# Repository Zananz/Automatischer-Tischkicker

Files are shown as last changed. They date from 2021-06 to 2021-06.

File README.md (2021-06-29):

<h1>Automatischer Tischkicker</h1>
<p>
1. <a href="https://github.com/Zananz/Automatischer-Tischkicker#beschreibung">Beschreibung</a><br>
2. <a href="https://github.com/Zananz/Automatischer-Tischkicker#funktionsweise">Funktionsweise</a><br>
3. <a href="https://github.com/Zananz/Automatischer-Tischkicker#anleitung">Anleitung</a><br>
</p>
<h2>Beschreibung</h2>
<p>Ein umgebauter Tischkicker welcher in der Lage ist Tore
automatisch zu zählen und Spielstände von bis zu 16 Spielern zu
Speichern.
</p>
<h2>Funktionsweise</h2>
<p>Der umgebaute Tischkicker verfügt über 2 Terminals mit jeweils
einem 2x16LCD-Display und 5 Schaltern. 4 der 5 Schalter dienen zur
Eingabe der Spieler-ID (ein max. vierstelliger Binärwert (0=0000,
1=0001 usw.)(daher 16 Spieler)), der verbleibende Schalter dient zum
bestätigen der ID.  Des weiten verfügt der Tischkicker über 2 rote
Buttons welche auf der jeweiligen Seite ein Tor (Punkt) abziehen.</p>
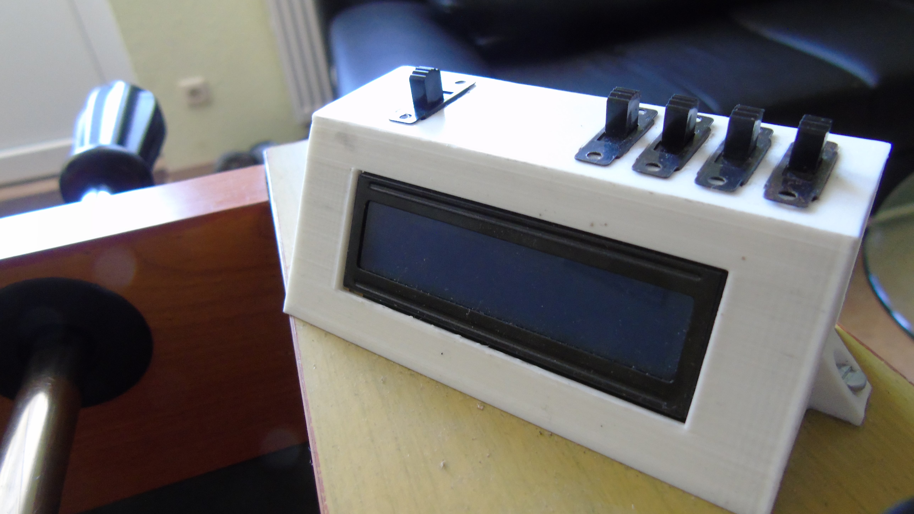
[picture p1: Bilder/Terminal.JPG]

<p>Tore werden mit Hilfe von Lichtschranken an der Ballführung
zwischen Tor und Ballausgabe gezählt.</p>
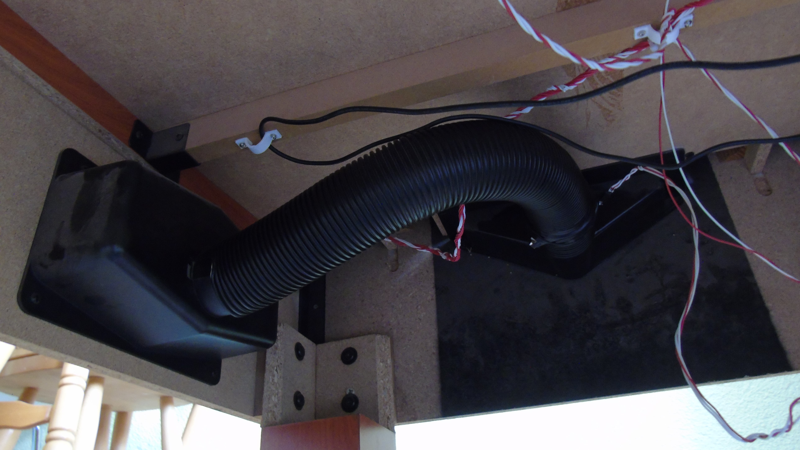
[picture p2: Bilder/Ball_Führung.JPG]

<p>Zur Ansteuerung der Komponenten wird ein Raspberry Pi pico verwendet welcher mit einer 3D-gedruckten <a href = "https://github.com/Zananz/Automatischer-Tischkicker/blob/main/3D-Modele/Halterung%20Platine.stl">Halterung</a> an der Unterseite des Tischkickers befestigt ist.</p>
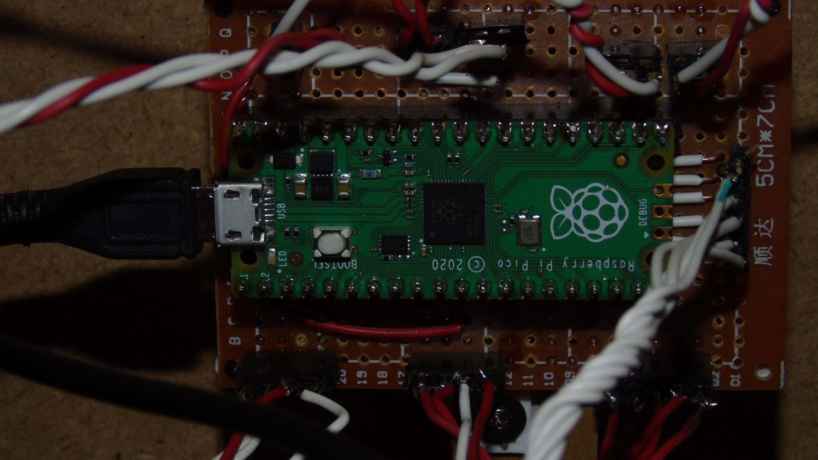
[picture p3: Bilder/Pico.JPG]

<h2>Anleitung</h2>
<h3>Hardware</h3>
<h4>Benötigt</h4>
<p>
&nbsp;&nbsp;&nbsp;&nbsp;1. <a href="https://www.reichelt.de/de/de/raspberry-pi-pico-rp2040-cortex-m0-microusb-rasp-pi-pico-p295706.html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">Raspberry Pi pico</a><br>
&nbsp;&nbsp;&nbsp;&nbsp;2. <a href="https://www.ebay.de/itm/353136370982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">2x 5V Laserdiode 6mm Ø</a><br>
&nbsp;&nbsp;&nbsp;&nbsp;3. <a href="https://www.ebay.de/itm/272853994103?chn=ps&mkevt=1&mkcid=28">2x Fotowiederstand</a><br>
&nbsp;&nbsp;&nbsp;&nbsp;4. <a href="https://www.ebay.de/itm/353160204184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">2x 16x2 LCD-Display + I2C Controller </a><br>
&nbsp;&nbsp;&nbsp;&nbsp;5. <a href="https://www.ebay.de/itm/333602388391?ssPageName=STRK%3AMEBIDX%3AIT&_trksid=p2060353.m2749.l2649">10x Schalter</a><br>
&nbsp;&nbsp;&nbsp;&nbsp;6. <a href="https://www.reichelt.de/arcade-button-mit-mikrostaster-rot-arc-button-rd-p225319.html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">2x Button 33mm Ø</a><br>
&nbsp;&nbsp;&nbsp;&nbsp;7. M3 Schrauben (4x 5mm, 4x ca.50mm), 4 Muttern<br>
&nbsp;&nbsp;&nbsp;&nbsp;8. <a href="https://www.ebay.de/itm/174035126580?chn=ps&mkevt=1&mkcid=28">Pin Header Male</a>, <a href="https://www.ebay.de/itm/174252775416?chn=ps&mkevt=1&mkcid=28">Pin Header Female</a><br>
&nbsp;&nbsp;&nbsp;&nbsp;9. <a href="https://www.ebay.de/itm/323649063851?chn=ps&mkevt=1&mkcid=28">50 x 70 mm Lochraster 2,54 mm Platine</a><br>
</p>
<h4>Verkablung</h4>
<table>
  <tr>
    <th>Pico Pin</th><th>LCD Spieler-1</th>
  </tr>
  <tr>
    <td>GND</td><td>GND</td>
  </tr>
  <tr>
    <td>V_BUS</td><td>V</td>
  </tr>
  <tr>
    <td>6</td><td>sda</td>
  </tr>
  <tr>
    <td>7</td><td>scl</td>
  </tr>
  <tr>
    <th>Pico Pin</th><th>LCD Spieler-2</th>
  </tr>
  <tr>
    <td>GND</td><td>GND</td>
  </tr>
  <tr>
    <td>V_BUS</td><td>V</td>
  </tr>
  <tr>
    <td>0</td><td>sda</td>
  </tr>
  <tr>
    <td>1</td><td>scl</td>
  </tr>
  <tr>
    <th>Pico</th><th>Lichtschranke Spieler-1 (siehe <a href="https://github.com/Zananz/Automatischer-Tischkicker#laserschranken">hier</a>)</th>
  </tr>
  <tr>
    <td>GND</td><td>GND</td>
  </tr>
  <tr>
    <td>3V3</td><td>3.3V</td>
  </tr>
  <tr>
    <td>ADC 0</td><td>Data</td>
  </tr>
  <tr>
    <th>Pico</th><th>Lichtschranke Spieler-2 (siehe <a href="https://github.com/Zananz/Automatischer-Tischkicker#laserschranken">hier</a>)</th>
  </tr>
  <tr>
    <td>GND</td><td>GND</td>
  </tr>
  <tr>
    <td>3V3</td><td>3.3V</td>
  </tr>
  <tr>
    <td>ADC 1</td><td>Data</td>
  </tr>
  <tr>
    <th>Pico Pin</th><th>Button Spieler-1</th>
  </tr>
  <tr>
    <td>V_BUS</td><td>Anschluss 1</td>
  </tr>
  <tr>
    <td>16</td><td>Anschluss 2</td>
  </tr>
  <tr>
    <th>Pico Pin</th><th>Button Spieler-2</th>
  </tr>
  <tr>
    <td>V_BUS</td><td>Anschluss 1</td>
  </tr>
  <tr>
    <td>17</td><td>Anschluss 2</td>
  </tr>
  <tr>
    <th>Pico Pin</th><th>Spielereingabe Spieler-1</th>
  </tr>
  <tr>
    <td>V_BUS</td><td>COM an allen Schaltern (SPDT)</td>
  </tr>
  <tr>
    <td>12</td><td>Schalter 1</td>
  </tr>
  <tr>
    <td>13</td><td>Schalter 2</td>
  </tr>
  <tr>
    <td>14</td><td>Schalter 3</td>
  </tr>
  <tr>
    <td>15</td><td>Schalter 4</td>
  </tr>
  <tr>
    <td>11</td><td>Schalter 5 (Login-Schalter)</td>
  </tr>
  <tr>
    <th>Pico Pin</th><th>Spielereingabe Spieler-2</th>
  </tr>
  <tr>
    <td>V_BUS</td><td>COM an allen Schaltern (SPDT)</td>
  </tr>
  <tr>
    <td>4</td><td>Schalter 1</td>
  </tr>
  <tr>
    <td>3</td><td>Schalter 2</td>
  </tr>
  <tr>
    <td>2</td><td>Schalter 3</td>
  </tr>
  <tr>
    <td>8</td><td>Schalter 4</td>
  </tr>
  <tr>
    <td>5</td><td>Schalter 5 (Login-Schalter)</td>
  </tr>
</table>
<h4>Laserschranke</h4>
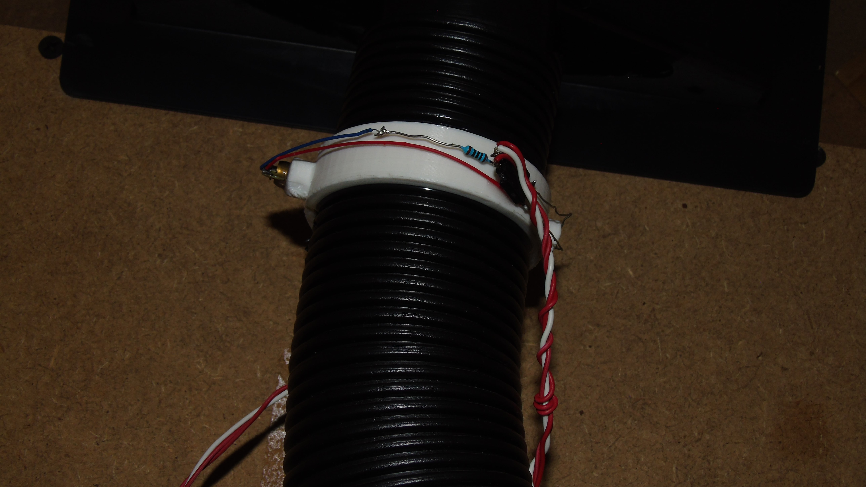
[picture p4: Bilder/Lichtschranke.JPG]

<p>
Die Lichtschranke besteht aus einer 3D-gedruckten Schelle in welche eine Laserdiode und ein Fotowiederstand geklebt wird. Diese liegen sich so gegenüber, dass der von der Diode ausgehende Lichtstrahl auf den Fotowiederstand trifft. Die Schelle wird so am Führungsschlauch des Balls angebracht, dass die für den Laser und den Fotowiederstand zu bohrenden Löcher den Ball nicht beim rollen behindern.<br>
Der Schaltplan für die Schranke:
</p>
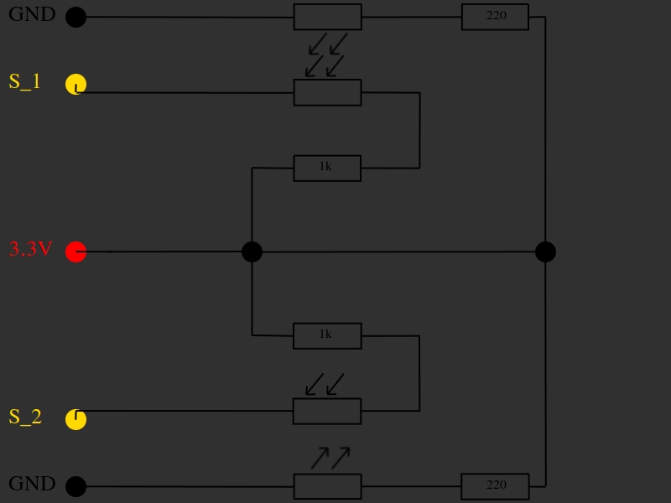
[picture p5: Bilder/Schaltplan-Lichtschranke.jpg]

<p>Wobei S_1 in der <a href="https://github.com/Zananz/Automatischer-Tischkicker#verkablung">Verkablungsübersicht</a> für Data (bei Butten Spieler-1) steht.(S_2 = Spieler-2)</p>
<h4>Bau</h4>
<p>
Terminal:<br>
&nbsp;&nbsp;&nbsp;&nbsp;1. Ausdruckern der Bauteile: <a href="https://github.com/Zananz/Automatischer-Tischkicker/blob/main/3D-Modele/Tischkicker_Station.stl">Station</a>, <a href="https://github.com/Zananz/Automatischer-Tischkicker/blob/main/3D-Modele/Abdeckung.stl">Abdeckung</a><br>
&nbsp;&nbsp;&nbsp;&nbsp;2. Einbauen der LCD-Display und der Schalter. (Verkabeln nach <a href="https://github.com/Zananz/Automatischer-Tischkicker#verkablung">Verkablungsübersicht</a>)<br>
</p>
<p>
Allgemein:
Alle Bauteile anbringen wie im Bild zu sehen. Mehr Bilder <a href="https://github.com/Zananz/Automatischer-Tischkicker/tree/main/Bilder">hier</a>.<br>
Zum bohren der Löcher für die Buttons wird ein 28mm Bohrer benätigt. Da die Terminals mit 2 M3 Schrauben befestigt werden wird ein 3,5mm Bohrer benötigt. Zu empfehlen ist weiterhin ein 10mm Bohrer zum bohren von Kabeldurchführungen an den Terminals.
</p>
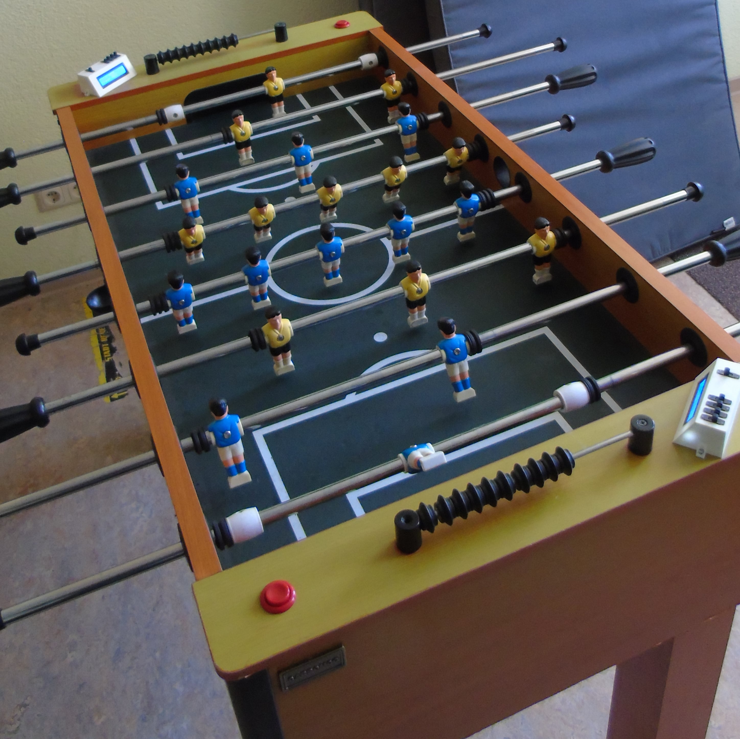
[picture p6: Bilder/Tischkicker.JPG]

<p>
Um den Pico auf der Platine an der Unterseite des Tischkickers zu befestigen wird eine 3D-gedruckte <a href="https://github.com/Zananz/Automatischer-Tischkicker/blob/main/3D-Modele/Halterung%20Platine.stl">Halterung</a> benötigt.<br>
Um den Pico mit Strom zu Versorgen ist es nicht ratsam dierekt mit einem USB-Kabel von einem Netzteil in der Steckdose an den USB-Eingang des Picos zu gehen, da es leit zu einem Defekt an diesem kommen kann wenn bspw. am Kabel gezogen wird. Es ist Empfehlenswert einen SStoßabfänger einzubauen. In diesem Fall ein an die Seitenwand geklebtes 12V DC Netzteil an welches ein 5V USB-Stepdown-Converter angeschlossen ist. Dies hat mehrere Vorteile zum einen wird zug am Kabel so am Netzteil "abgefangen" zum anderen besteht die Möglichkeit sein Smarphone am Tischkicker zu Laden.
</p>
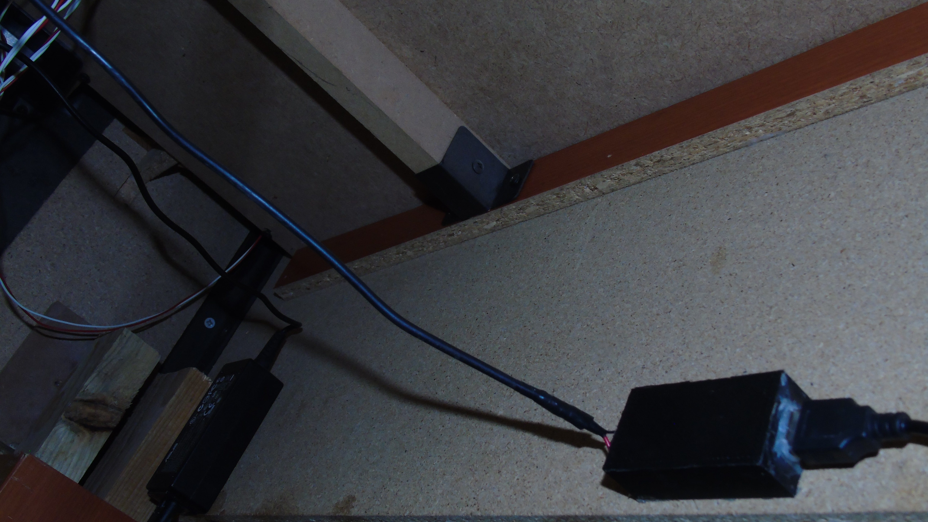
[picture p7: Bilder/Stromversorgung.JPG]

<p>
Sind alle Bauteile angebracht und Verkabelt, ist der Bau abgeschlossen.
</p>
<h3>Software</h3>
<p>
Alle .py Dateien aus dem Repo müssen auf den Pico gepielt werden.<br>
Es muss ein Ordner "Spielstände" auf dem Pico erstellt werden. Ist dies geschehen muss Spielstände_auf_0.py ausgeführt werden. Wurde das Skript ausgeführt sollten im Ordner "Spielstände" Textdateien im Muster "4ställigeBinärzahl-4ställigeBinärzahl.txt" vorzufinden sein. Ist dies der Fall ist der Tischkicker einsatzbereit. Bei ausführung von main.py (starten des Picos) wird das Programm zur steuerung des Tischkickers ausgeführt.
</p>
<h4>Spielernamen</h4>
<p>Von Zeile 2-17 in main.py befinden sich die Namenszuweisungen, um bsp.w Spieler_4 den Namen Bob zuzuweisen muss "Spieler_4 = "Frei_3"" in "Spieler_4 = "Bob"" geändert werden.</p>
<h4>Fehlerbehebung Lichtschranke</h4>
<p>Sollten dauerhaft Tore gezählt werden ist es ratsam die in main.py ab Zeile 19 befindlichen Grenzwerte der Lichtschranken zu senken.(Diese sellen ACD().read_u16() Werte da) Die Grenzwerte können je nach verwendeten Bauteilen variieren.</p>

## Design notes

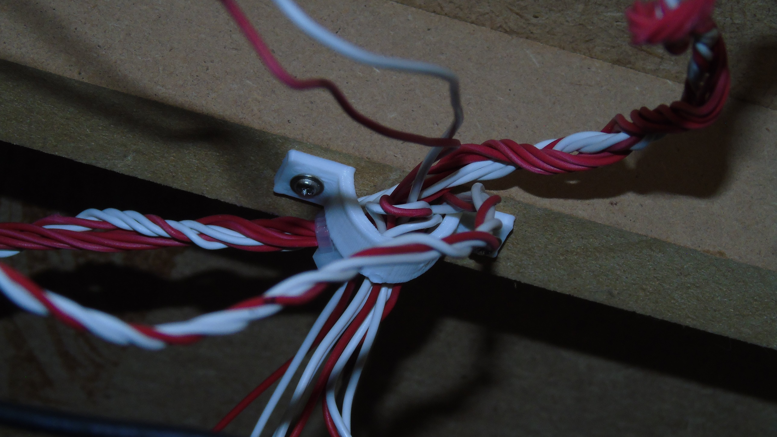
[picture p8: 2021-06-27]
Bilder/Kabelhalter.JPG

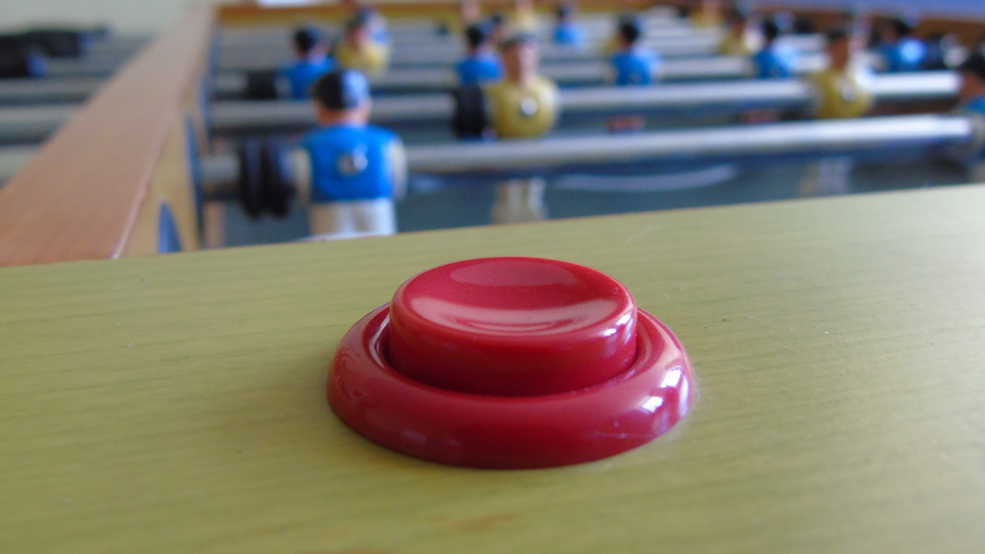
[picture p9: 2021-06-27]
Bilder/Button.JPG

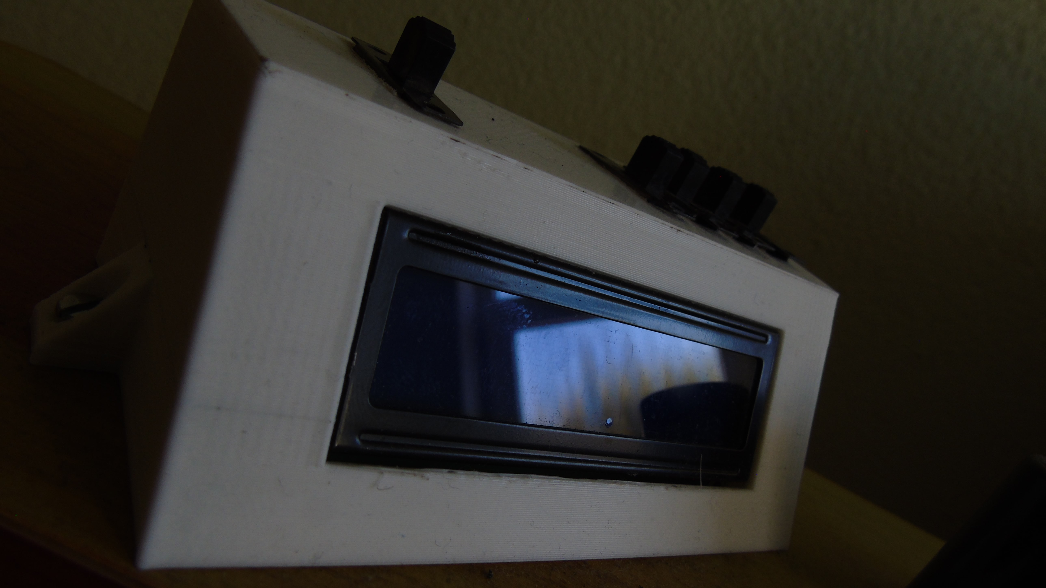
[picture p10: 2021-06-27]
Bilder/Terminal _1.JPG

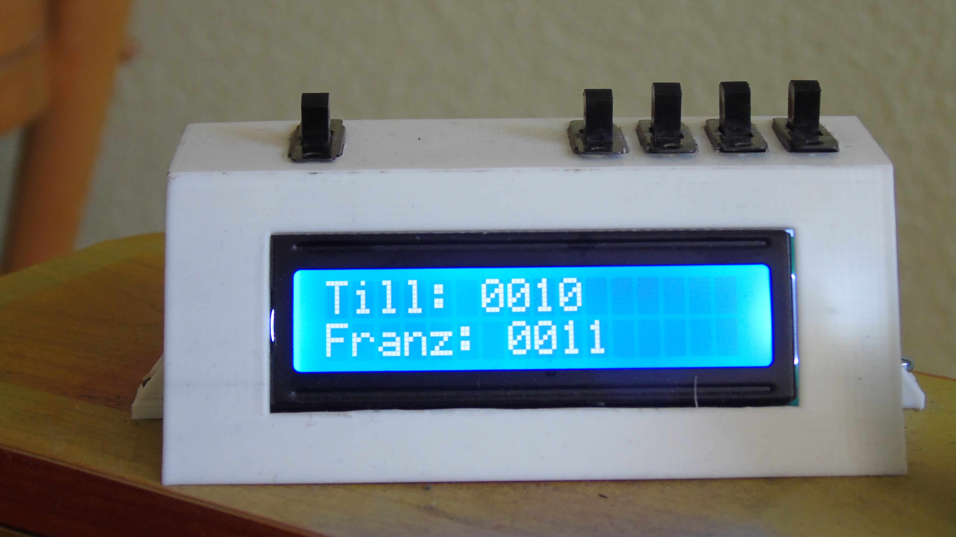
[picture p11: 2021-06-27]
Bilder/Spieler-ID.JPG

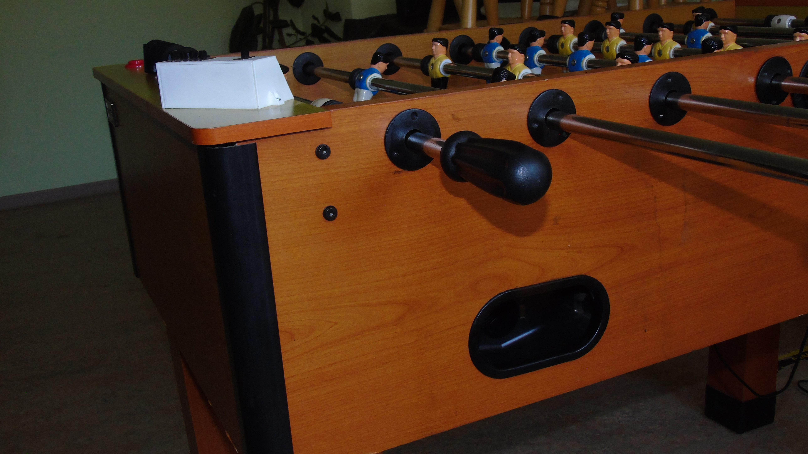
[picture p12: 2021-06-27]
Bilder/Seitlicher-Ausgang.JPG

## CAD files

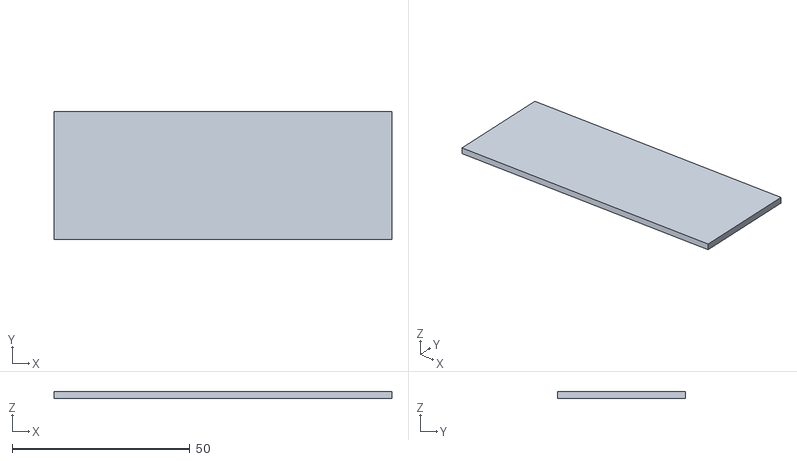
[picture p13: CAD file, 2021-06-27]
3D-Modele/Abdeckung.stl
95.0 x 36.0 x 2.00

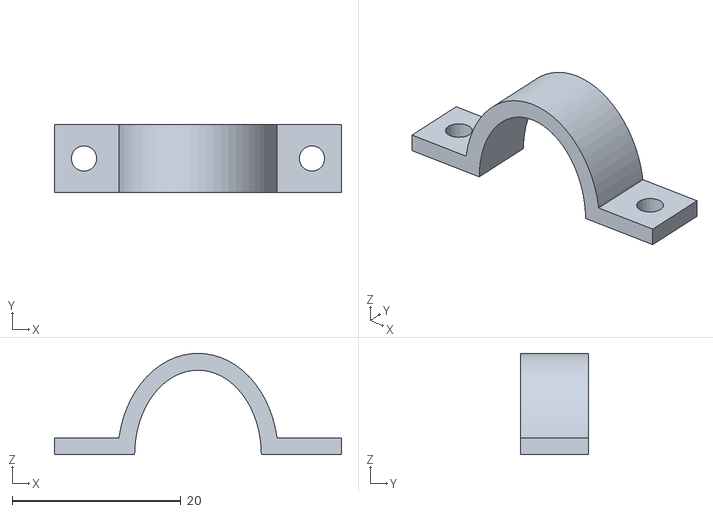
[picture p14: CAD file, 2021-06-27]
3D-Modele/Kabel Leiter.stl
34.0 x 8.00 x 12.0

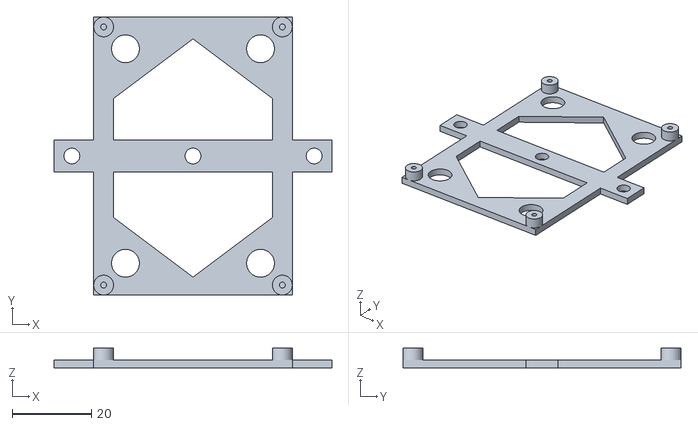
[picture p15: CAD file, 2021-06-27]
3D-Modele/Halterung Platine.stl
70.0 x 70.0 x 5.00

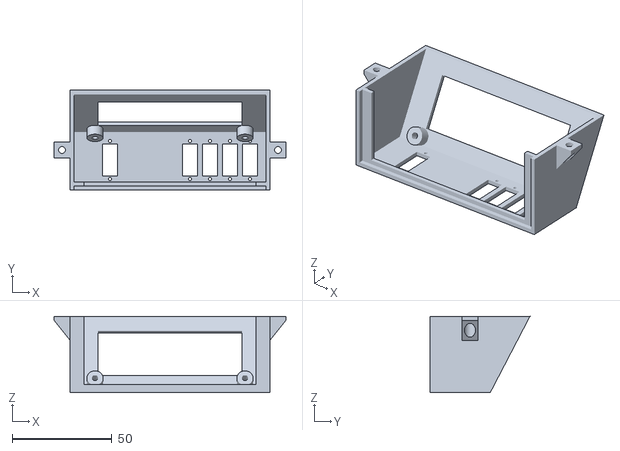
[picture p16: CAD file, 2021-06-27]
3D-Modele/Tischkicker_Station.stl
116.0 x 50.0 x 38.2

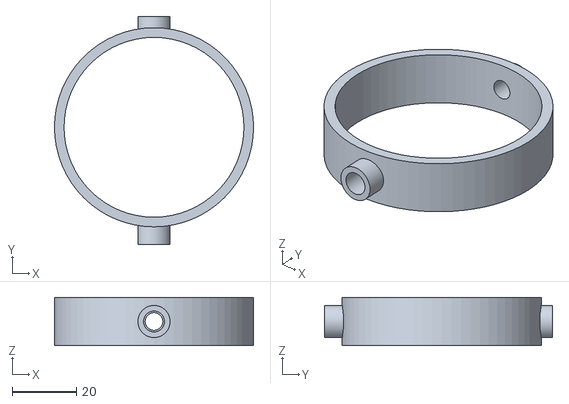
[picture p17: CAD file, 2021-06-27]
3D-Modele/Verstärkte Schelle.stl
62.0 x 71.0 x 15.0

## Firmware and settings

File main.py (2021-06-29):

#Anzupassen:
Spieler_1  = "Gast_1"	#0000
Spieler_2  = "Frei_1"	#0001
Spieler_3  = "Frei_2"	#0010
Spieler_4  = "Frei_3"	#0011
Spieler_5  = "Frei_4"	#0100
Spieler_6  = "Frei_5"	#0101
Spieler_7  = "Frei_6"	#0110
Spieler_8  = "Frei_7"	#0111
Spieler_9  = "Frei_8"	#1000
Spieler_10 = "Frei_9"	#1001
Spieler_11 = "Frei_10" #1010
Spieler_12 = "Frei_11" #1011
Spieler_13 = "Frei_12" #1100
Spieler_14 = "Frei_13" #1101
Spieler_15 = "Frei_14" #1110
Spieler_16 = "Gast_2"  #1111

lichtschranke_1_grenzwert = 30000
lichtschranke_2_grenzwert = 30000


from machine import I2C, Pin
import time
from machine_i2c_lcd import I2cLcd
import bauteile as bt

lichtschranke_1 = bt.Lichtschranke(0, lichtschranke_1_grenzwert)
lichtschranke_2 = bt.Lichtschranke(1, lichtschranke_2_grenzwert)

i2c_1 = I2C(1,sda=Pin(6), scl=Pin(7),freq = 400000)
i2c_2 = I2C(0,sda=Pin(0), scl=Pin(1),freq = 400000)

lcd_1 = I2cLcd(i2c_1, 39, 2, 16)
lcd_2 = I2cLcd(i2c_2, 39, 2, 16)
    
Spieler_Eingabe_1 = bt.Spieler_Eingabe(12,13,14,15,11)
Spieler_Eingabe_2 = bt.Spieler_Eingabe(4,3,2,8,5)

Minus_Button_1 = bt.Minus_Button(16)
Minus_Button_2 = bt.Minus_Button(17)

spieler_liste = {"0000":Spieler_1, "0001":Spieler_2, "0010":Spieler_3, "0011":Spieler_4, "0100":Spieler_5, "0101":Spieler_6, "0110":Spieler_7, "0111":Spieler_8, "1000":Spieler_9, "1001":Spieler_10, "1010":Spieler_11, "1011":Spieler_12, "1100":Spieler_13, "1101":Spieler_14, "1110":Spieler_15, "1111":Spieler_16}

def auf_spiel_warten(Spieler_Eingabe_1, Spieler_Eingabe_2, spieler_liste, lcd_1, lcd_2):
    
    keine_eingaben = True
    zähler = 0
    
    while keine_eingaben:
        
        if Spieler_Eingabe_1.gib_spieler() != None and Spieler_Eingabe_2.gib_spieler() != None:
            
            lcd_1.clear()
            lcd_2.clear()
            
            keine_eingaben = False
            
            return True #um spiel zu starten
            
        else:
            lcd_1.clear()
            lcd_2.clear()
            
            lcd_1.move_to(0,0)
            lcd_1.putstr("%s: %s"%(list(spieler_liste.values())[zähler], list(spieler_liste.keys())[zähler]))
            
            lcd_1.move_to(0,1)
            lcd_1.putstr("%s: %s"%(list(spieler_liste.values())[zähler+1], list(spieler_liste.keys())[zähler+1]))
            
            lcd_2.move_to(0,0)
            lcd_2.putstr("%s: %s"%(list(spieler_liste.values())[zähler+2], list(spieler_liste.keys())[zähler+2]))
          
            lcd_2.move_to(0,1)
            lcd_2.putstr("%s: %s"%(list(spieler_liste.values())[zähler+3], list(spieler_liste.keys())[zähler+3]))
            
            zähler += 4
            
            if zähler == 16:
                zähler = 0
                
            time.sleep(2)
            
def spiel(Spieler_Eingabe_1, Spieler_Eingabe_2, spieler_liste, lcd_1, lcd_2, lichtschranke_1, lichtschranke_2):
    
    spieler_kürzel_1 = Spieler_Eingabe_1.gib_spieler()#umgekehrt da denkfehler bei der instalation
    spieler_kürzel_2 = Spieler_Eingabe_2.gib_spieler() #umkehrung keinen effekt auf restlichhen code  
    
    if spieler_kürzel_1 != spieler_kürzel_2:
        
        lcd_1.move_to(0,0)
        lcd_1.putstr("%s vs %s"%(spieler_liste[spieler_kürzel_1], spieler_liste[spieler_kürzel_2]))
        
        lcd_1.move_to(0,1)
        lcd_1.putstr("0 : 0")
        
        lcd_2.move_to(0,0)
        lcd_2.putstr("%s vs %s"%(spieler_liste[spieler_kürzel_2], spieler_liste[spieler_kürzel_1]))
        
        lcd_2.move_to(0,1)
        lcd_2.putstr("0 : 0")
        
        spiel = True
        
        tor_zähler_1 = 0
        tor_zähler_2 = 0
        
        while spiel:
            
            if lichtschranke_1.treffer():
                
                tor_zähler_1 += 1
                
                if tor_zähler_1 >= 10:
                    
                    lcd_1.clear()
                    lcd_2.clear()
                    
                    lcd_1.move_to(0,0)
                    lcd_1.putstr("Gewonnen %s"%spieler_liste[spieler_kürzel_1])
                    
                    lcd_2.move_to(0,0)
                    lcd_2.putstr("Gewonnen %s"%spieler_liste[spieler_kürzel_1])
                    
                    sec_zähler = 15 #zeit um letzen punkt zurück zu nehmen
                    
                    while sec_zähler > 0:
                        
                        lcd_1.move_to(0,1)
                        lcd_1.putstr("%i "%sec_zähler)
                        
                        lcd_2.move_to(0,1)
                        lcd_2.putstr("%i "%sec_zähler)
                        
                        time.sleep(1)
                        
                        if Minus_Button_1.ist_gedrückt():
                            
                            sec_zähler = 0
                            
                            tor_zähler_1 = 9
                            
                            lcd_1.move_to(0,0)
                            lcd_1.putstr("%s vs %s"%(spieler_liste[spieler_kürzel_1], spieler_liste[spieler_kürzel_2]))
                            
                            lcd_2.move_to(0,0)
                            lcd_2.putstr("%s vs %s"%(spieler_liste[spieler_kürzel_2], spieler_liste[spieler_kürzel_1]))
                            
                            lcd_1.move_to(0,1)
                            lcd_1.putstr("%i : %i"%(tor_zähler_1, tor_zähler_2))
                            
                            lcd_2.move_to(0,1)
                            lcd_2.putstr("%i : %i"%(tor_zähler_2, tor_zähler_1))
                            
                            while Minus_Button_1.ist_gedrückt():
                                #um nur 1 tor abzuziehen
                                time.sleep_ms(50)
                                
                        sec_zähler -= 1
                                
                    if tor_zähler_1 == 10:
                        
                        spiel = False
                        
                        tor_zähler_1 = 0
                        tor_zähler_2 = 0
                        
                        #Abspeichern des gesammtspielstandes
                        #2 Dateien um später lesen zu erleichten (Speicher nicht problematisch)
                        text_dokument = open("Spielstände/%s-%s.txt"%(spieler_kürzel_1, spieler_kürzel_2), "r")
                        alter_stand = text_dokument.read()
                        text_dokument.close()
                        
                        text_dokument = open("Spielstände/%s-%s.txt"%(spieler_kürzel_1, spieler_kürzel_2), "w")#2. öffnen um alen inhalt zu löschen
                        text_dokument.write("%s:%s"%(str(int(alter_stand.split(":")[0])+1), str(alter_stand.split(":")[1])))
                        text_dokument.close()
                        
                        #2.Datei
                        text_dokument = open("Spielstände/%s-%s.txt"%(spieler_kürzel_2, spieler_kürzel_1), "r")
                        alter_stand = text_dokument.read()
                        text_dokument.close()
                        
                        text_dokument = open("Spielstände/%s-%s.txt"%(spieler_kürzel_2, spieler_kürzel_1), "w")#2. öffnen um alen inhalt zu löschen
                        text_dokument.write("%s:%s"%(str(alter_stand.split(":")[0]), str(int(alter_stand.split(":")[1])+1)))
                        text_dokument.close()
                        
                        lcd_1.clear()
                        lcd_2.clear()
                            
                        lcd_1.move_to(0,0)
                        lcd_1.putstr("Spielstand:")
                            
                        lcd_2.move_to(0,0)
                        lcd_2.putstr("Spielstand:")
                            
                        text_dokument = open("Spielstände/%s-%s.txt"%(spieler_kürzel_1, spieler_kürzel_2), "r")
                        stand_1 = text_dokument.read()
                        text_dokument.close()
                            
                        text_dokument = open("Spielstände/%s-%s.txt"%(spieler_kürzel_2, spieler_kürzel_1), "r")
                        stand_2 = text_dokument.read()
                        text_dokument.close()
                            
                        lcd_1.move_to(0,1)
                        lcd_1.putstr("%s:%s"%(stand_1.split(":")[0], stand_1.split(":")[1]))
                                         
                        lcd_2.move_to(0,1)
                        lcd_2.putstr("%s:%s"%(stand_2.split(":")[0], stand_2.split(":")[1]))
                        
                        
                        sec_zähler = 7 #zeit des anzeigen des spielstandes
                        
                        while sec_zähler > 0:
                                         
                            sec_zähler -= 1
                                         
                            time.sleep(1)
                            
                        lcd_1.clear()
                        lcd_2.clear()
                            
                        lcd_1.move_to(0,0)
                        lcd_1.putstr("Neustart in:")
                            
                        lcd_2.move_to(0,0)
                        lcd_2.putstr("Neustart in:")
                        
                        if Spieler_Eingabe_1.gib_spieler() != None or Spieler_Eingabe_2.gib_spieler() != None:
                        
                            sec_zähler = 15 #zeit um Neustart abzubrechen
                    
                            while sec_zähler > 0:
                                
                                lcd_1.move_to(0,1)
                                lcd_1.putstr("%i "%sec_zähler)
                                
                                lcd_2.move_to(0,1)
                                lcd_2.putstr("%i "%sec_zähler)
                                
                                sec_zähler -=1
                                
                                if Spieler_Eingabe_1.gib_spieler() == None or Spieler_Eingabe_2.gib_spieler() == None:
                                    
                                    sec_zähler = 0
                                
                                time.sleep(1)
                else:
                    
                    lcd_1.move_to(0,1)
                    lcd_1.putstr("%i : %i  "%(tor_zähler_1, tor_zähler_2))
                    
                    lcd_2.move_to(0,1)
                    lcd_2.putstr("%i : %i  "%(tor_zähler_2, tor_zähler_1))
                    
                    time.sleep(1)
            
                
            if lichtschranke_2.treffer():
                
                tor_zähler_2 += 1
                
                if tor_zähler_2 >= 10:
                    
                    lcd_1.clear()
                    lcd_2.clear()
                    
                    lcd_1.move_to(0,0)
                    lcd_1.putstr("Gewonnen %s"%spieler_liste[spieler_kürzel_2])
                    
                    lcd_2.move_to(0,0)
                    lcd_2.putstr("Gewonnen %s"%spieler_liste[spieler_kürzel_2])
                    
                    sec_zähler = 15 #zeit um letzen punkt zurück zu nehmen
                    
                    while sec_zähler > 0:
                        
                        lcd_1.move_to(0,1)
                        lcd_1.putstr("%i "%sec_zähler)
                        
                        lcd_2.move_to(0,1)
                        lcd_2.putstr("%i "%sec_zähler)
                        
                        time.sleep(1)
                        
                        if Minus_Button_2.ist_gedrückt():
                            
                            sec_zähler = 0
                            
                            tor_zähler_2 = 9
                            
                            lcd_1.move_to(0,0)
                            lcd_1.putstr("%s vs %s"%(spieler_liste[spieler_kürzel_1], spieler_liste[spieler_kürzel_2]))
                            
                            lcd_2.move_to(0,0)
                            lcd_2.putstr("%s vs %s"%(spieler_liste[spieler_kürzel_2], spieler_liste[spieler_kürzel_1]))
                            
                            lcd_1.move_to(0,1)
                            lcd_1.putstr("%i : %i"%(tor_zähler_1, tor_zähler_2))
                            
                            lcd_2.move_to(0,1)
                            lcd_2.putstr("%i : %i"%(tor_zähler_2, tor_zähler_1))
                            
                            while Minus_Button_2.ist_gedrückt():
                                #um nur 1 tor abzuziehen
                                time.sleep_ms(50)
                                
                        sec_zähler -= 1
                                
                    if tor_zähler_2 == 10:
                        
                        spiel = False
                        
                        tor_zähler_1 = 0
                        tor_zähler_2 = 0
                        
                        #Abspeichern des gesammtspielstandes
                        #2 Dateien um später lesen zu erleichten (Speicher nicht problematisch)
                        text_dokument = open("Spielstände/%s-%s.txt"%(spieler_kürzel_1, spieler_kürzel_2), "r")
                        alter_stand = text_dokument.read()
                        text_dokument.close()
                        
                        text_dokument = open("Spielstände/%s-%s.txt"%(spieler_kürzel_1, spieler_kürzel_2), "w")#2. öffnen um alen inhalt zu löschen
                        text_dokument.write("%s:%s"%(str(alter_stand.split(":")[0]), str(int(alter_stand.split(":")[1])+1)))
                        text_dokument.close()
                        
                        #2.Datei
                        text_dokument = open("Spielstände/%s-%s.txt"%(spieler_kürzel_2, spieler_kürzel_1), "r")
                        alter_stand = text_dokument.read()
                        text_dokument.close()
                        
                        text_dokument = open("Spielstände/%s-%s.txt"%(spieler_kürzel_2, spieler_kürzel_1), "w")#2. öffnen um alen inhalt zu löschen
                        text_dokument.write("%s:%s"%(str(int(alter_stand.split(":")[0])+1), str(alter_stand.split(":")[1])))
                        text_dokument.close()
                        
                        lcd_1.clear()
                        lcd_2.clear()
                            
                        lcd_1.move_to(0,0)
                        lcd_1.putstr("Spielstand:")
                            
                        lcd_2.move_to(0,0)
                        lcd_2.putstr("Spielstand:")
                            
                        text_dokument = open("Spielstände/%s-%s.txt"%(spieler_kürzel_1, spieler_kürzel_2), "r")
                        stand_1 = text_dokument.read()
                        text_dokument.close()
                            
                        text_dokument = open("Spielstände/%s-%s.txt"%(spieler_kürzel_2, spieler_kürzel_1), "r")
                        stand_2 = text_dokument.read()
                        text_dokument.close()
                            
                        lcd_1.move_to(0,1)
                        lcd_1.putstr("%s:%s"%(stand_1.split(":")[0], stand_1.split(":")[1]))
                                         
                        lcd_2.move_to(0,1)
                        lcd_2.putstr("%s:%s"%(stand_2.split(":")[0], stand_2.split(":")[1]))
                        
                        
                        sec_zähler = 7 #zeit des anzeigen des spielstandes
                        
                        while sec_zähler > 0:
                                         
                            sec_zähler -= 1
                                         
                            time.sleep(1)
                        
                        if Spieler_Eingabe_1.gib_spieler() != None or Spieler_Eingabe_2.gib_spieler() != None:
                            
                            lcd_1.clear()
                            lcd_2.clear()
                                
                            lcd_1.move_to(0,0)
                            lcd_1.putstr("Neustart in:")
                                
                            lcd_2.move_to(0,0)
                            lcd_2.putstr("Neustart in:")
                        
                            sec_zähler = 15 #zeit um Neustart abzubrechen
                        
                            while sec_zähler > 0:
                                
                                lcd_1.move_to(0,1)
                                lcd_1.putstr("%i "%sec_zähler)
                                
                                lcd_2.move_to(0,1)
                                lcd_2.putstr("%i "%sec_zähler)
                                
                                sec_zähler -=1
                                
                                if Spieler_Eingabe_1.gib_spieler() == None or Spieler_Eingabe_2.gib_spieler() == None:
                                    
                                    sec_zähler = 0
                                
                                time.sleep(1)
                else:
                
                    lcd_1.move_to(0,1)
                    lcd_1.putstr("%i : %i  "%(tor_zähler_1, tor_zähler_2))
                    
                    lcd_2.move_to(0,1)
                    lcd_2.putstr("%i : %i  "%(tor_zähler_2, tor_zähler_1))
                    
                    time.sleep(1)
                
                
            if Minus_Button_1.ist_gedrückt():
                
                if tor_zähler_1 > -99: #um zu großen Wert zu verhindern
                
                    tor_zähler_1 -= 1
                    
                    lcd_1.move_to(0,1)
                    lcd_1.putstr("%i : %i"%(tor_zähler_1, tor_zähler_2))
                    
                    lcd_2.move_to(0,1)
                    lcd_2.putstr("%i : %i"%(tor_zähler_2, tor_zähler_1))
                    
                while Minus_Button_1.ist_gedrückt():
                    #um nur 1 tor pro druck abzuziehen bzw. loop ohne pause zu verhindern
                    time.sleep_ms(50)
                    
                    if  Minus_Button_2.ist_gedrückt(): #um spiel abzubrechen
                        
                        if Spieler_Eingabe_1.gib_spieler() == None and Spieler_Eingabe_2.gib_spieler() == None:
                            spiel = False
            
            if Minus_Button_2.ist_gedrückt():
                
                if tor_zähler_2 > -99: #um zu großen Wert zu verhindern
                    
                    tor_zähler_2 -= 1
                    
                    lcd_1.move_to(0,1)
                    lcd_1.putstr("%i : %i"%(tor_zähler_1, tor_zähler_2))
                    
                    lcd_2.move_to(0,1)
                    lcd_2.putstr("%i : %i"%(tor_zähler_2, tor_zähler_1))
                
                while Minus_Button_2.ist_gedrückt():
                    #um nur 1 tor pro druck abzuziehen bzw. loop ohne pause zu verhindern
                    time.sleep_ms(50)
                    
                    if  Minus_Button_1.ist_gedrückt(): #um spiel abzubrechen
                        
                        if Spieler_Eingabe_1.gib_spieler() == None and Spieler_Eingabe_2.gib_spieler() == None:
                            spiel = False
        
        time.sleep_us(50)
        
    else:
        
        lcd_1.clear()
        lcd_2.clear()
                
        lcd_1.move_to(0,0)
        lcd_1.putstr("Fehler erkannt:")
                
        lcd_2.move_to(0,0)
        lcd_2.putstr("Fehler erkannt:")
                
        lcd_1.move_to(0,1)
        lcd_1.putstr("2x %s"%spieler_kürzel_1)
                
        lcd_2.move_to(0,1)
        lcd_2.putstr("2x %s"%spieler_kürzel_1)
        
        time.sleep(1)
        
while True:
    
    if auf_spiel_warten(Spieler_Eingabe_1, Spieler_Eingabe_2, spieler_liste, lcd_1, lcd_2):
        spiel(Spieler_Eingabe_1, Spieler_Eingabe_2, spieler_liste, lcd_1, lcd_2, lichtschranke_1, lichtschranke_2)

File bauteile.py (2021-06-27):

#Klassen für physische bauteile

from machine import ADC #für lichtschranke (photoresitor)

from machine import Pin #für Schalter und Taster

class Lichtschranke(): #ball unterbricht diese wenn: tor
    
    def __init__(self, pin, grenzwert):
        
        self.pin = ADC(pin)
        self.grenzwert = grenzwert #Spannungen der Lichtschranken variert leicht (unterschiede in ele. Bauteilen) 
        
    def treffer(self): # gibt true für treffer zurück
        
        wert = self.pin.read_u16()
    
        if wert > self.grenzwert: 
            return False
        else:
            return True
        
class Spieler_Eingabe(): # 4 Schalter zur eingabe, 1 Schalter zum bestätigen
    
    def __init__(self, pin_1, pin_2, pin_3, pin_4, pin_5):
        
        self.pin_1 = Pin(pin_1, Pin.IN, Pin.PULL_DOWN)
        self.pin_2 = Pin(pin_2, Pin.IN, Pin.PULL_DOWN)
        self.pin_3 = Pin(pin_3, Pin.IN, Pin.PULL_DOWN)
        self.pin_4 = Pin(pin_4, Pin.IN, Pin.PULL_DOWN)
        
        self.pin_5 = Pin(pin_5, Pin.IN, Pin.PULL_DOWN)
        
    def gib_spieler(self): #gibt str mit 4 stelliger binärzahl oder None zurück
        
        if self.pin_5.value() == 1:
            return "%i%i%i%i"%(self.pin_1.value(), self.pin_2.value(), self.pin_3.value(), self.pin_4.value())
        else:
            return None
        
class Minus_Button(): #Taster um ein tor der jewaligen seite zu löschen
    
    def __init__(self, pin):
        
        self.pin = Pin(pin, Pin.IN, Pin.PULL_DOWN)
        
    def ist_gedrückt(self): #gibt True oder False zurück
        
        return bool(self.pin.value())
        
